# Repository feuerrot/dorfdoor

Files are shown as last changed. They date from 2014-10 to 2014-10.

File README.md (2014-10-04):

# Türsteuerung
Can haz digitale Türsteuerung mit verschiedenen Inputs und Statusleds und
foo? Ja!

Die [Tür des Chaosdorf](https://wiki.chaosdorf.de/Chaosdoor) hat einen 
eingebauten Motor von Fuhr - den Multitronic 881 und da alle Funkanwendungen
(insbesondere der Funk-Fingerabdrucksensor) auf unbekannter Technik basieren
und damit erstmal als für einen Hackerspace ungeeignet gelten, muss man das
natürlich selber bauen.

## History
v1 umfasste eine Lochrasterplatine mit AVR ATMega8, der über Optokoppler den
Potentialfreien Eingang des Türmotors ansteuerte. Ein Problem war unter
anderem, dass der komplette Öffnungs- und Schließvorgang incl. Verriegeln
dazu führte, dass nach gerade mal 3 Jahren ein Zahnrad brach.

Die aktuelle v2 mit 'lag halt rum' AVR ATMega88PA trennt eigentliche
Steuerung und Boardinterface auf zwei Platinen auf. Der Mikrocontroller ist
zusammen mit der verbundenen Seagate Dockstar und passendem Netzteil für
alles und Tür in einem Gehäuse. Die Ansteuerung der Tür und das damit
verbundene Problem bleibt bestehen.

[@penma](https://github.com/penma) hat aber dankenswerterweise das
Protokoll der Tür im für unseren Zweck ausreichenden Maße reverse
engineered, um die gewünschte Tagesfallenfunktion auch ohne Zusatzplatine
für wahrscheinlich mehrere hunderte Euro zu erlangen.
Bei v2 wird dafür der Optokoppler für die Tagesfalle genutzt.

## Schaltplan

### μC-Platine
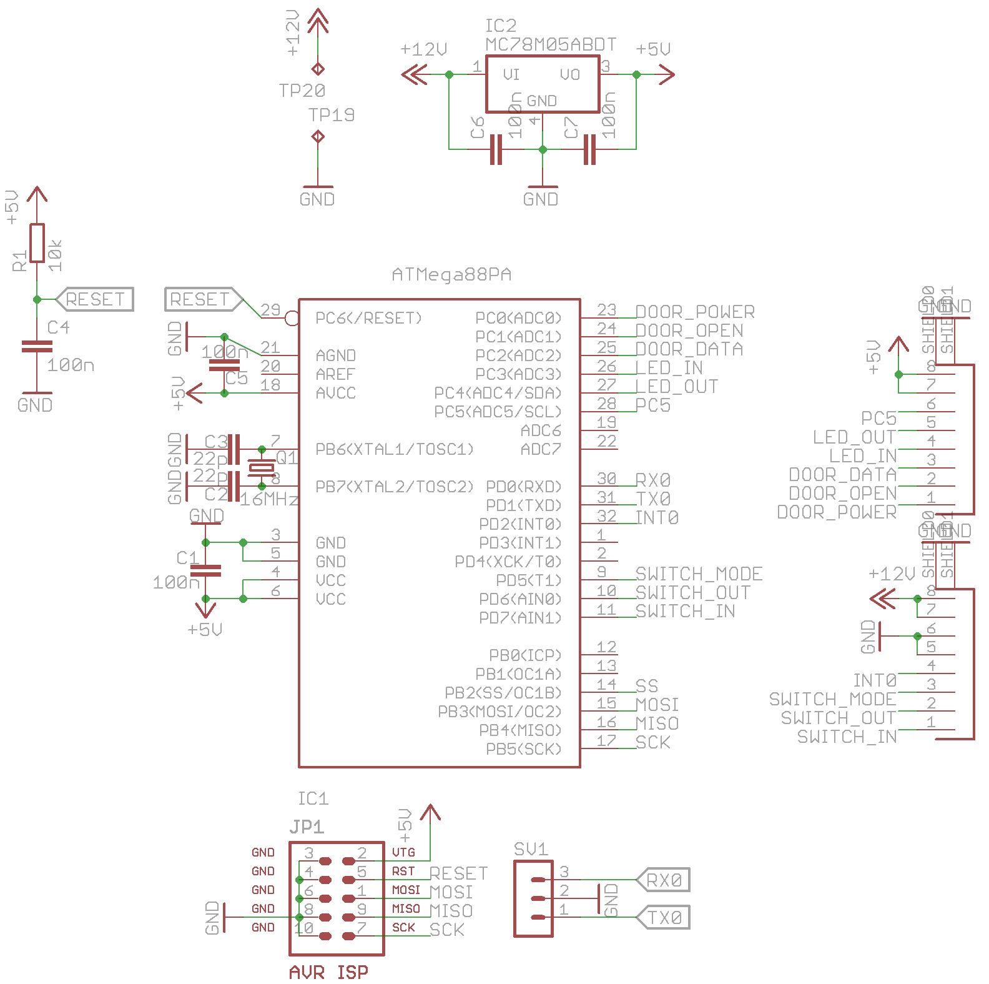
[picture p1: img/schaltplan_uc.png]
Schaltplan der μC-Platine


### IO-Platine
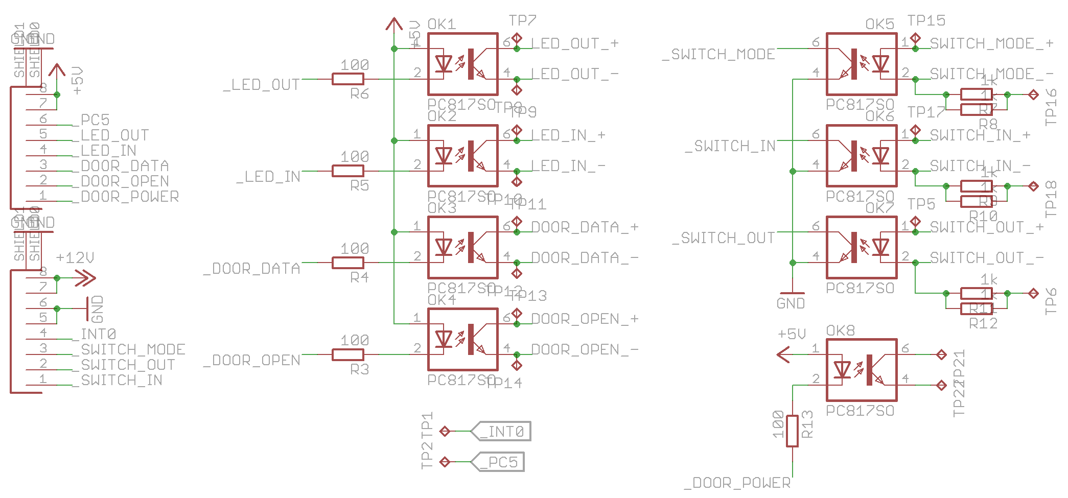
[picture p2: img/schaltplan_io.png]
Schaltplan der IO-Platine


## Layout

### μC-Platine
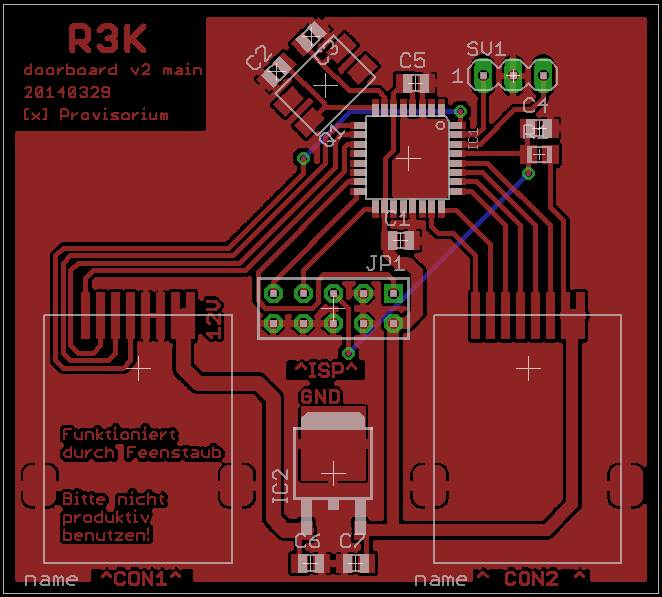
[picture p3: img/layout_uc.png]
Layout der μC-Platine


### IO-Platine
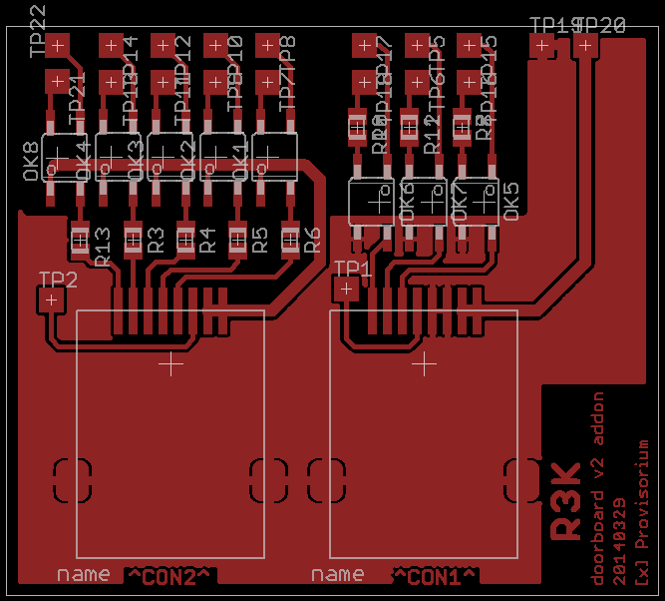
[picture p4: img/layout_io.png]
Layout der IO-Platine


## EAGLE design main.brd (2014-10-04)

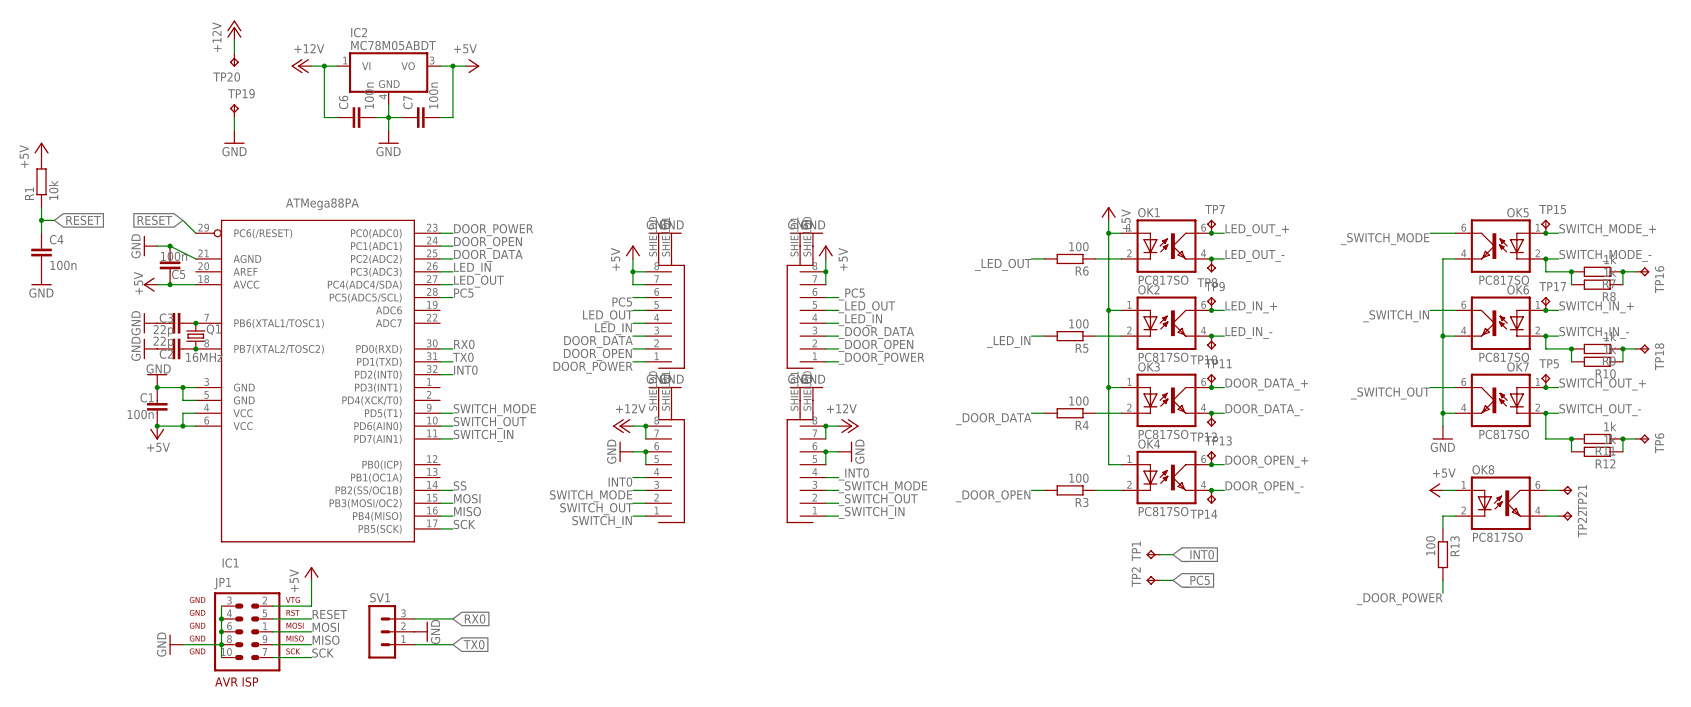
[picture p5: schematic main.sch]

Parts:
C1, C4, C5, C6, C7: 100n; C0805
C2, C3: 22p; C0805
CON1, CON1_, CON2, CON2_: 451000
IC1: ATMega88PA; TQFP32-08
IC2: MC78M05ABDT; DPACK_3
JP1: AVR-ISP-10
OK1, OK2, OK3, OK4, OK5, OK6, OK7, OK8: PC817SO; SO4
Q1: 16MHz; MQ
R1: 10k; M0805
R3, R4, R5, R6, R13: 100; M0805
R7, R8, R9, R10, R11, R12: 1k; M0805
SV1: MA03-1
TP1, TP2, TP5, TP6, TP7, TP8, TP9, TP10, TP11, TP12, TP13, TP14, TP15, TP16, TP17, TP18, TP19, TP20, TP21, TP22: TPTP20SQ; TP20SQ

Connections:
+5V: C1.1, C5.1, C7.2, CON2.7, CON2.8, CON2_.7, CON2_.8, IC1.4 (VCC), IC1.6 (VCC), IC1.18 (AVCC), IC2.3 (VO), JP1.2, OK1.1 (A), OK2.1 (A), OK3.1 (A), OK4.1 (A), OK8.1 (A), R1.2
+12V: C6.1, CON1.7, CON1.8, CON1_.7, CON1_.8, IC2.1 (VI), TP20.TP
DOOR_DATA: CON2.3, IC1.25 (PC2(ADC2))
DOOR_DATA_+: OK3.6 (COL), TP11.TP
DOOR_DATA_-: OK3.4 (EMIT), TP12.TP
DOOR_OPEN: CON2.2, IC1.24 (PC1(ADC1))
DOOR_OPEN_+: OK4.6 (COL), TP13.TP
DOOR_OPEN_-: OK4.4 (EMIT), TP14.TP
DOOR_POWER: CON2.1, IC1.23 (PC0(ADC0))
GND: C1.2, C2.1, C3.1, C4.2, C5.2, C6.2, C7.1, CON1.5, CON1.6, CON1.SHIELD0, CON1.SHIELD1, CON1_.5, CON1_.6, CON1_.SHIELD0, CON1_.SHIELD1, CON2.SHIELD0, CON2.SHIELD1, CON2_.SHIELD0, CON2_.SHIELD1, IC1.3 (GND), IC1.5 (GND), IC1.21 (AGND), IC2.4 (GND), JP1.3, JP1.4, JP1.6, JP1.8, JP1.10, OK5.4 (EMIT), OK6.4 (EMIT), OK7.4 (EMIT), SV1.2, TP19.TP
INT0: CON1.4, IC1.32 (PD2(INT0))
LED_IN: CON2.4, IC1.26 (PC3(ADC3))
LED_IN_+: OK2.6 (COL), TP9.TP
LED_IN_-: OK2.4 (EMIT), TP10.TP
LED_OUT: CON2.5, IC1.27 (PC4(ADC4/SDA))
LED_OUT_+: OK1.6 (COL), TP7.TP
LED_OUT_-: OK1.4 (EMIT), TP8.TP
MISO: IC1.16 (PB4(MISO)), JP1.9
MOSI: IC1.15 (PB3(MOSI/OC2)), JP1.1
unnamed: OK8.2 (C), R13.1
unnamed: OK4.2 (C), R3.1
unnamed: C3.2, IC1.7 (PB6(XTAL1/TOSC1)), Q1.P3 (2)
unnamed: C2.2, IC1.8 (PB7(XTAL2/TOSC2)), Q1.P1 (1)
unnamed: OK3.2 (C), R4.1
unnamed: OK2.2 (C), R5.1
unnamed: OK1.2 (C), R6.1
unnamed: R7.1, R8.1, TP16.TP
unnamed: R11.1, R12.1, TP6.TP
unnamed: R9.1, R10.1, TP18.TP
unnamed: OK8.6 (COL), TP21.TP
unnamed: OK8.4 (EMIT), TP22.TP
PC5: CON2.6, IC1.28 (PC5(ADC5/SCL))
RESET: C4.1, IC1.29 (PC6(/RESET)), JP1.5, R1.1
RX0: IC1.30 (PD0(RXD)), SV1.3
SCK: IC1.17 (PB5(SCK)), JP1.7
SS: IC1.14 (PB2(SS/OC1B))
SWITCH_IN: CON1.1, IC1.11 (PD7(AIN1))
SWITCH_IN_+: OK6.1 (A), TP17.TP
SWITCH_IN_-: OK6.2 (C), R9.2, R10.2
SWITCH_MODE: CON1.3, IC1.9 (PD5(T1))
SWITCH_MODE_+: OK5.1 (A), TP15.TP
SWITCH_MODE_-: OK5.2 (C), R7.2, R8.2
SWITCH_OUT: CON1.2, IC1.10 (PD6(AIN0))
SWITCH_OUT_+: OK7.1 (A), TP5.TP
SWITCH_OUT_-: OK7.2 (C), R11.2, R12.2
TX0: IC1.31 (PD1(TXD)), SV1.1
_DOOR_DATA: CON2_.3, R4.2
_DOOR_OPEN: CON2_.2, R3.2
_DOOR_POWER: CON2_.1, R13.2
_INT0: CON1_.4, TP1.TP
_LED_IN: CON2_.4, R5.2
_LED_OUT: CON2_.5, R6.2
_PC5: CON2_.6, TP2.TP
_SWITCH_IN: CON1_.1, OK6.6 (COL)
_SWITCH_MODE: CON1_.3, OK5.6 (COL)
_SWITCH_OUT: CON1_.2, OK7.6 (COL)

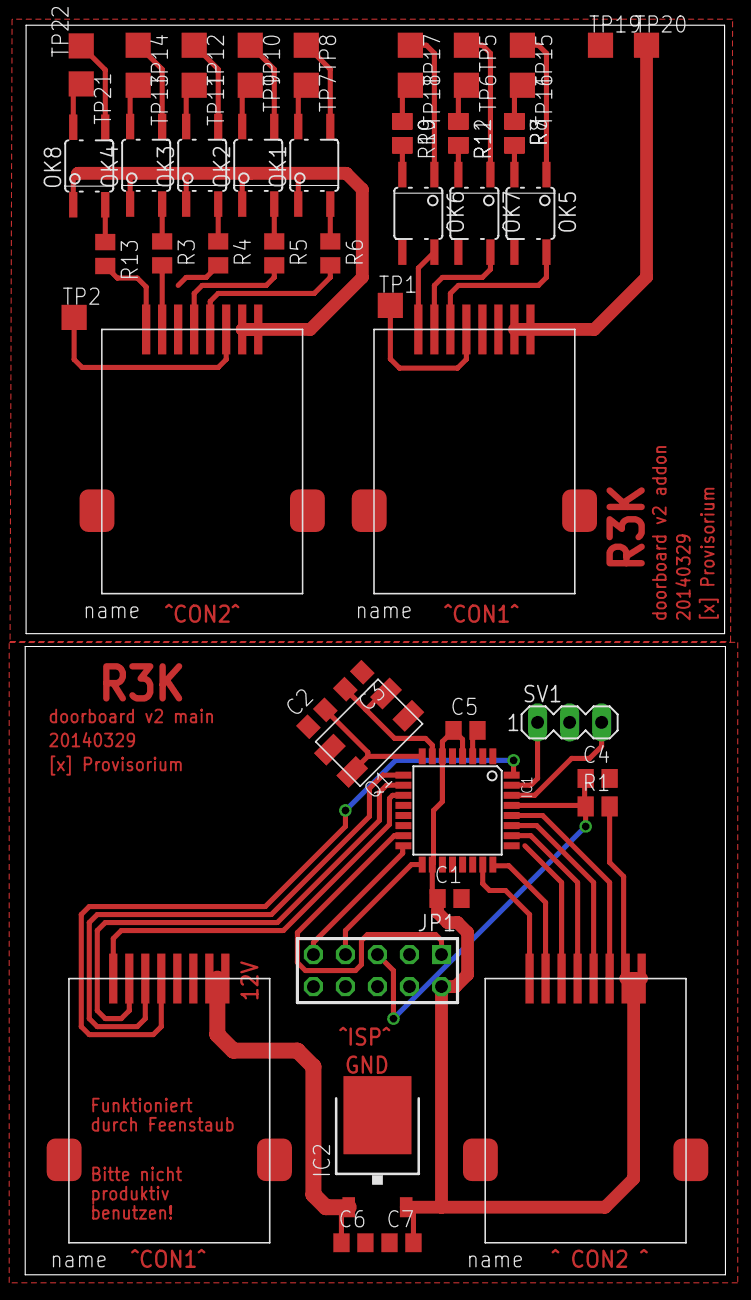
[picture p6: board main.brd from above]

Board: 2 copper layers, 55.5 x 99.1 mm, 56 parts (0 on the bottom side), 55 nets.

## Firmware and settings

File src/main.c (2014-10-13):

// coding: utf-8
#include <avr/io.h>
#include <avr/interrupt.h>
#include <avr/wdt.h>
#include <util/delay.h>
#include "rs232.h"

char resettext[]	=	"p";	// power on
char openhs[]		=	"o";	// hackerspace open
char closedhs[]		=	"c";	// hackerspace closed
char dooror1[]		=	"1";	// ssh stage 1
char dooror2[]		=	"2";	// ssh stage 2
char dooror3[]		=	"e";	// ssh error
char dooropened[]	=	"s";	// open via switch
char bell[]		=	"b";	// bell
char resetof[]		=	"r";	// ssh stage reset
char statuso[]		=	"SO";
char statusc[]		=	"SC";

volatile uint8_t resetoverflow;
uint8_t toggledoor;
#define DOORTOGGLE 20

#define SWITCH_RED	PD2 // Taster Rot
#define SWITCH_GREEN	PD5 // Taster Grün
#define SWITCH_OUT	PD6
#define SWITCH_IN	PD7
#define DOOR_DATA	PC2
#define DOOR_POWER	PC0
#define DOOR_OPEN	PC1
#define LED_OUT		PC4 // normale LED im Außentaster
#define LED_IN		PC3 // sind die WS2812b

volatile struct {
	unsigned dooropenstage1:1;
	unsigned dooropenstage2:1;
	unsigned openhackerspace:1;
	unsigned openhackerspaceold:1;
	unsigned bell:1;
} flags;

#define CMD_OPEN_LOCK      0x10cd
#define CMD_OPEN_TF        0x11d0
#define CMD_OPEN_TF_HOLD   0x12f7
#define CMD_LOCK           0x14b9
#define CMD_UNLOCK         0x179e

void ws2812bit(uint8_t bit){
	PORTC |= (1<<LED_IN);
	if (bit){
		_delay_us(0.85);
		PORTC &= ~(1<<LED_IN);
		_delay_us(0.35);
	} else {
		_delay_us(0.35);
		PORTC &= ~(1<<LED_IN);
		_delay_us(0.85);
	}
}

void led_r(void){
	for (int i=7; i>=0; i--){
		ws2812bit(0);
	}
	for (int i=7; i>=0; i--){
		ws2812bit(1);
	}
	for (int i=7; i>=0; i--){
		ws2812bit(0);
	}
}

void led_g(void){
	for (int i=7; i>=0; i--){
		ws2812bit(1);
	}
	for (int i=13; i>=0; i--){
		ws2812bit(0);
	}
}


static void send_door_halfbit(int v) {
	if (!v) {
		PORTC &= ~(1 << DOOR_DATA);
	} else {
		PORTC |= (1 << DOOR_DATA);
	}
	_delay_us(500);
}

static void send_door_cmd(uint16_t word) {
	cli();

	for (int rep = 1; rep <= 11; rep++) {
		send_door_halfbit(0);

		for (signed int i = 15; i >= 0; i--) {
			if (word & ((uint16_t)1 << i)) {
				/* bit set */
				send_door_halfbit(1);
				send_door_halfbit(0);
			} else {
				send_door_halfbit(0);
				send_door_halfbit(1);
			}
		}

		/* release bus */
		send_door_halfbit(1);

		/* packet delay */
		_delay_us(2500);
	}

	sei();
}

void setled(uint8_t led){
	cli();
	if (led){
		PORTC &= ~(1<<LED_OUT);
		led_g();
		led_g();
		led_g();
	} else {
		PORTC |= (1<<LED_OUT);
		led_r();
		led_r();
		led_r();
	}
	sei();
}

void opendoor(void){
	if (flags.openhackerspace) {
		send_door_cmd(CMD_OPEN_TF);
	} else {
		send_door_cmd(CMD_OPEN_LOCK);
	}
	_delay_ms(100);
	_serputs(dooropened);
}

uint8_t input(uint8_t flag){
	return (!(PIND & (1<<flag)));
}

void init(void){
	_usart_init();

	/* Protipp:
	 * Der Defaultzustand von PORT- und DDR-Registern ist 0x00.
	 * D.h.: Schaltfunktion bei Output = low ist eine scheiß Idee.
	 *
	 * Hier fixen wir das, indem wir erstmal einen Pullup machen und
	 * dann den Pin auf high schalten.
	 */
	PORTC |= (1<<DOOR_OPEN);
	DDRC  |= (1<<DOOR_OPEN);

	DDRC  |= (1<<DOOR_DATA)|(1<<DOOR_POWER)|(1<<LED_OUT)|(1<<LED_IN);
	PORTC |= (1<<DOOR_DATA)|(1<<LED_OUT)|(1<<LED_IN);

	PORTD |= (1<<SWITCH_GREEN)|(1<<SWITCH_RED)|(1<<SWITCH_OUT)|(1<<SWITCH_IN);

	_delay_ms(10);
	TCCR2B |= (1<<CS22)|(1<<CS21);
	TIMSK2 |= (1<<TOIE2);

	setled(0);

	sei();
	_serputs(resettext);
}

int main(void) {
	init();

	while(1) {
		if (flags.openhackerspace != flags.openhackerspaceold){
			flags.openhackerspaceold = flags.openhackerspace;
			if (flags.openhackerspace){
				send_door_cmd(CMD_UNLOCK);
				setled(1);
				_serputs(openhs);
			} else {
				send_door_cmd(CMD_LOCK);
				setled(0);
				_serputs(closedhs);
			}
		}
		if (flags.openhackerspace){
			if (input(SWITCH_IN) | input(SWITCH_OUT)){
				setled(0);
				_delay_ms(50);
				setled(1);
				opendoor();
				setled(0);
				_delay_ms(50);
				setled(1);
			}
		} else {
			if ((input(SWITCH_IN) | input(SWITCH_OUT)) && flags.bell == 0){
				_serputs(bell);
				flags.bell = 1;
				//Klingelfunktion
			}
		}
		if (flags.dooropenstage2){
			_serputs(dooror2);
			flags.dooropenstage2 = 0;
			opendoor();
		}

		if (input(SWITCH_GREEN)|input(SWITCH_RED)){
			toggledoor++;
		} else {
			toggledoor = 0;
		}
		if (toggledoor > DOORTOGGLE){
			if ((flags.openhackerspace == 0 && input(SWITCH_GREEN))||(flags.openhackerspace == 1 && input(SWITCH_RED))){
				flags.openhackerspace ^= 1;
			}
			toggledoor = 0;
		}

		_delay_ms(100);
	}
	return 0;
}

ISR(USART_RX_vect){
    uint8_t chr = UDR0;
    switch (chr){
		case 'r':
		       	wdt_enable(WDTO_1S);
			break;
		case 'd':
			if (flags.dooropenstage1){
				_serputs(dooror3);
			} else {
				flags.dooropenstage1 = 1;
				_serputs(dooror1);
			}
			break;
		case 'b':
			if (flags.dooropenstage1){
				flags.dooropenstage2 = 1;
				flags.dooropenstage1 = 0;
			} else {
				_serputs(dooror3);
			}
			break;
		case 'o':
			flags.openhackerspace = 1;
			break;
		case 'c':
			flags.openhackerspace = 0;
			break;
		case 's':
			if (flags.openhackerspace){
				_serputs(statuso);
			} else {
				_serputs(statusc);
			}
		default:
			flags.dooropenstage1 = 0;
			break;
    }
}

ISR(TIMER2_OVF_vect){
	if (resetoverflow == 0){
		flags.dooropenstage1 = 0;
		flags.dooropenstage2 = 0;
		flags.bell = 0;
		_serputs(resetof);
	}
	resetoverflow++;
}

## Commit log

2012-03-31 Rückmeldungen auf ein Zeichen angepasst, aber noch mit \n
    Muss noch schöner werden und so…
2012-04-01 Manuelle Steuerung über Taster eingebaut
    * 2 Sekunden drücken zum togglen des Status (auf<->zu)
    * Der Code ist immernoch weird
    * Andere LEDs ausmachen, dass nur eine leuchtet oder alle zusammen leuchten?
    * Pythonscript, das auf dem host läuft mit rein.
2012-04-02 Alle LEDs ändern ihren Status
    Da derzeit nur eine LED genutzt wird, zeigen die anderen LEDs genau das
    gleiche an, um Nutzer nach einer Änderung zu verwirren.
2014-09-28 what? ahrgs, das ist ja grottig. Alles neu schreiben…
2014-10-04 add layout and schematic
    [main.brd, main.sch]
2014-10-04 add fuse settings and program-fuse to makefile
2014-10-04 adding images of the current version
    [main.brd, main.sch]
2014-10-04 Optokoppler für Daymode => Optokoppler für Datenleitung
    [main.brd, main.sch]
2014-10-11 ws2812b dreckig und hoffentlich funktionierend einbinden
2014-10-11 Da sind 3 Leds drin und nicht nur eine.
2014-10-11 + cli();sei(); um die LED-Ansteuerung, weil timing
2014-10-11 s/SWITCH_MODE/SWITCH_GREEN/ und beide Taster eingebaut
2014-10-13 set led on powerup
